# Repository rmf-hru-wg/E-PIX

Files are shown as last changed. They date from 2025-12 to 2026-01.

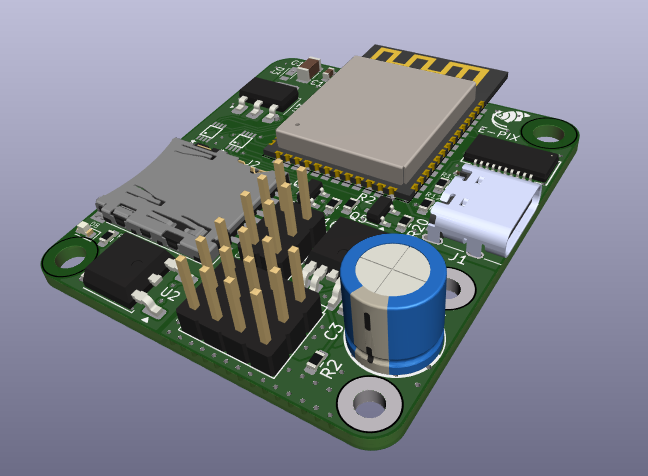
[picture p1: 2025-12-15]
E-PIX/img_front.png

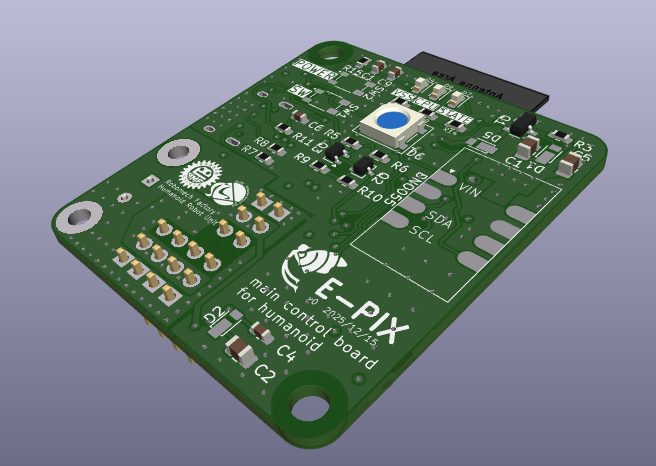
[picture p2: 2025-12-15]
E-PIX/img_back.png

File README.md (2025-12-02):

# Control Board 1

## スペック

- ESP32C3@160MHz WiFi+BT5(BT Classicは非対応)
- ICS変換 × 2
- ADC × 2
- BTS6142D 保護回路+ロードスイッチ
- 9DoF IMU AE-BNO055を裏面に搭載可能

## 設計指針

- できるだけ安く　1000円以下
- できるだけ小さく　40mm×40mm
- ICS変換基板の小型化　10mm×8mm
- 無線を使った遠隔操作　WiFi 2.4GHz IEEE 802.11b/g/n

## 今後の方針

- CPUをラズパイなどにして計算性能やカメラの搭載
- ROS2と繋げる

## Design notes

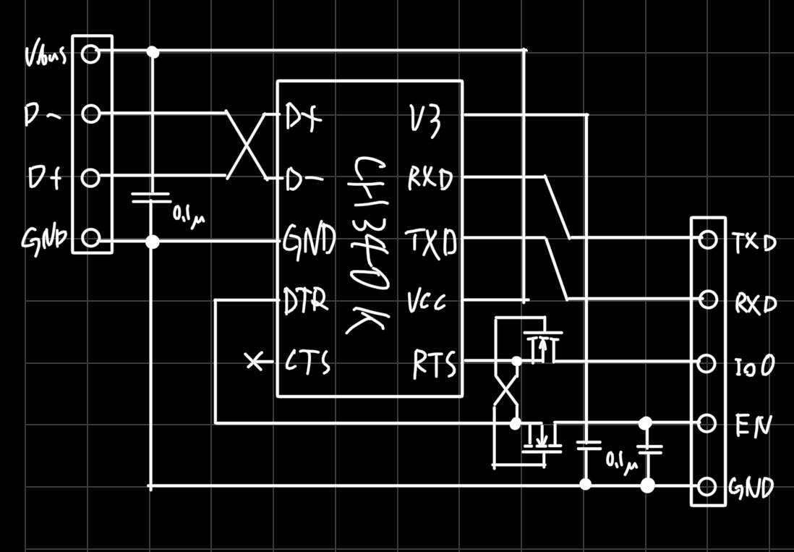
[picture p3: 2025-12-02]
DataSheets/Board/esp32-ch340k.jpeg

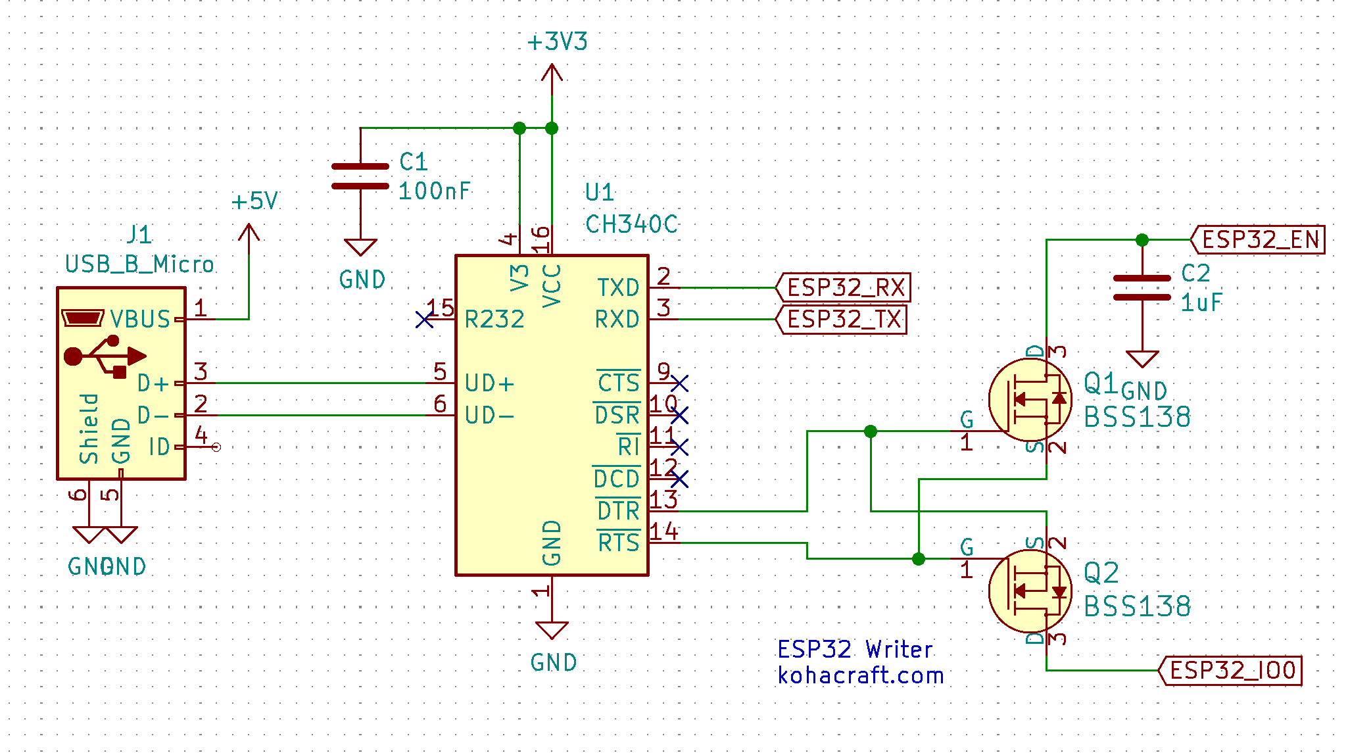
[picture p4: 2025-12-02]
DataSheets/Board/esp32ch340.png

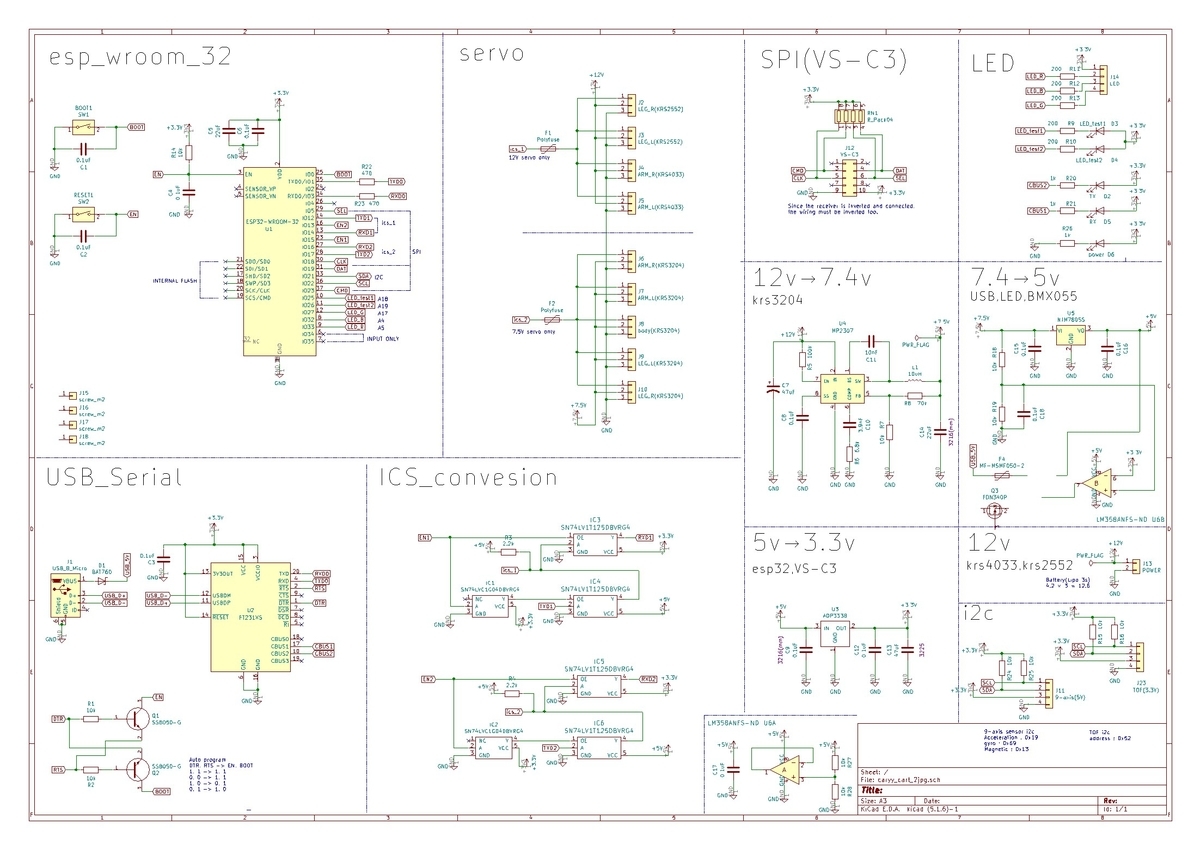
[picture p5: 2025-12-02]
DataSheets/Board/ESP32Kondo.jpg

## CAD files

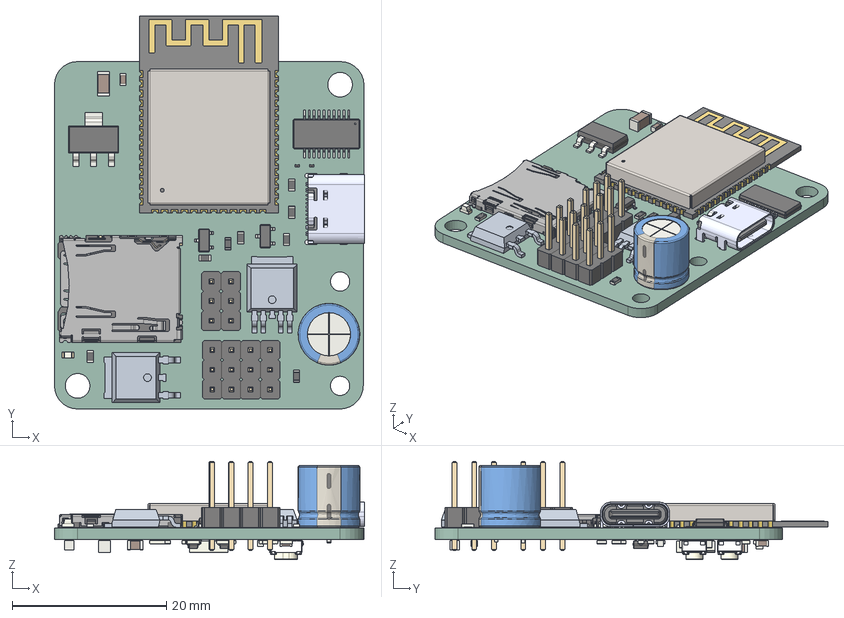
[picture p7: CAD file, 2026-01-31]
E-PIX/E-PIX.step
40.2 x 50.9 x 12.7 mm
C_1206_3216Metric x 2
R_0603_1608Metric x 13
microSD_HC_Hirose_DM3AT-SF-PEJM5
C_0201_0603Metric x 2
C_0603_1608Metric x 6
LED_0603_1608Metric x 3
5077CR-16-SMC2-BK-TR
E-PIX 1.12.1
SOT-23 x 2
C0201_20210301.STEP^C0201_20210301.STEP_Submodel-C0201_part_ DesignRootModel_PCB_ESP32-S3-WROOM-1_V1(2)_PCB_ESP32-S3-WROOM-1_V1 x 14
L0201_20210301.STEP^L0201_20210301.STEP_Submodel-L0201_part_ DesignRootModel_PCB_ESP32-S3-WROOM-1_V1(2)_PCB_ESP32-S3-WROOM-1_V1 x 3
C0402_20210301.STEP^C0402_20210301.STEP_Submodel-C0402_part_ DesignRootModel_PCB_ESP32-S3-WROOM-1_V1(2)_PCB_ESP32-S3-WROOM-1_V1
R0201_20210301.STEP^R0201_20210301.STEP_Submodel-R0201_part_ DesignRootModel_PCB_ESP32-S3-WROOM-1_V1(2)_PCB_ESP32-S3-WROOM-1_V1 x 8
trace_1^Submodel-MINI-ANT-TYPEB_668419613_part_DesignRootModel_PCB_ ESP32-S3-WROOM-1_V1(2)_PCB_ESP32-S3-WROOM-1_V1
DFN1006.STEP^DFN1006.STEP_Submodel-SOD882_part_DesignRootModel_PCB_ ESP32-S3-WROOM-1_V1(2)_PCB_ESP32-S3-WROOM-1_V1
SOP8_rev1_20210308.STEP^SOP8_rev1_20210308.STEP_Submodel-SOP8_1P27_6P6_ part_DesignRootModel_PCB_ESP32-S3-WROOM-1_V1(2)_PCB_ESP32-S3-WROOM-1_V1
XTAL3225_20210301.STEP^XTAL3225_20210301.STEP_Submodel-XTAL3225_part_ DesignRootModel_PCB_ESP32-S3-WROOM-1_V1(2)_PCB_ESP32-S3-WROOM-1_V1
ESP32-S3_20210301.STEP^ESP32-S3_20210301.STEP_Submodel-QFN56_0P4_7_ part_DesignRootModel_PCB_ESP32-S3-WROOM-1_V1(2)_PCB_ESP32-S3-WROOM-1_V1
uid__4-128^DesignRootModel_PCB_ESP32-S3-WROOM-1_V1(2)_PCB_ ESP32-S3-WROOM-1_V1
uid__4-129^DesignRootModel_PCB_ESP32-S3-WROOM-1_V1(2)_PCB_ ESP32-S3-WROOM-1_V1
uid__4-130^DesignRootModel_PCB_ESP32-S3-WROOM-1_V1(2)_PCB_ ESP32-S3-WROOM-1_V1
uid__4-149^DesignRootModel_PCB_ESP32-S3-WROOM-1_V1(2)_PCB_ ESP32-S3-WROOM-1_V1
uid__4-150^DesignRootModel_PCB_ESP32-S3-WROOM-1_V1(2)_PCB_ ESP32-S3-WROOM-1_V1
uid__4-151^DesignRootModel_PCB_ESP32-S3-WROOM-1_V1(2)_PCB_ ESP32-S3-WROOM-1_V1
uid__4-167^DesignRootModel_PCB_ESP32-S3-WROOM-1_V1(2)_PCB_ ESP32-S3-WROOM-1_V1
uid__4-168^DesignRootModel_PCB_ESP32-S3-WROOM-1_V1(2)_PCB_ ESP32-S3-WROOM-1_V1
uid__4-169^DesignRootModel_PCB_ESP32-S3-WROOM-1_V1(2)_PCB_ ESP32-S3-WROOM-1_V1
uid__1-279^DesignRootModel_PCB_ESP32-S3-WROOM-1_V1(2)_PCB_ ESP32-S3-WROOM-1_V1
uid__1-280^DesignRootModel_PCB_ESP32-S3-WROOM-1_V1(2)_PCB_ ESP32-S3-WROOM-1_V1
uid__1-292^DesignRootModel_PCB_ESP32-S3-WROOM-1_V1(2)_PCB_ ESP32-S3-WROOM-1_V1
uid__1-298^DesignRootModel_PCB_ESP32-S3-WROOM-1_V1(2)_PCB_ ESP32-S3-WROOM-1_V1
uid__1-299^DesignRootModel_PCB_ESP32-S3-WROOM-1_V1(2)_PCB_ ESP32-S3-WROOM-1_V1
uid__1-300^DesignRootModel_PCB_ESP32-S3-WROOM-1_V1(2)_PCB_ ESP32-S3-WROOM-1_V1
uid__1-301^DesignRootModel_PCB_ESP32-S3-WROOM-1_V1(2)_PCB_ ESP32-S3-WROOM-1_V1
uid__1-304^DesignRootModel_PCB_ESP32-S3-WROOM-1_V1(2)_PCB_ ESP32-S3-WROOM-1_V1
uid__1-305^DesignRootModel_PCB_ESP32-S3-WROOM-1_V1(2)_PCB_ ESP32-S3-WROOM-1_V1
uid__1-308^DesignRootModel_PCB_ESP32-S3-WROOM-1_V1(2)_PCB_ ESP32-S3-WROOM-1_V1
uid__1-310^DesignRootModel_PCB_ESP32-S3-WROOM-1_V1(2)_PCB_ ESP32-S3-WROOM-1_V1
uid__1-311^DesignRootModel_PCB_ESP32-S3-WROOM-1_V1(2)_PCB_ ESP32-S3-WROOM-1_V1
uid__1-325^DesignRootModel_PCB_ESP32-S3-WROOM-1_V1(2)_PCB_ ESP32-S3-WROOM-1_V1
uid__1-334^DesignRootModel_PCB_ESP32-S3-WROOM-1_V1(2)_PCB_ ESP32-S3-WROOM-1_V1
uid__1-338^DesignRootModel_PCB_ESP32-S3-WROOM-1_V1(2)_PCB_ ESP32-S3-WROOM-1_V1
uid__1-339^DesignRootModel_PCB_ESP32-S3-WROOM-1_V1(2)_PCB_ ESP32-S3-WROOM-1_V1
uid__1-340^DesignRootModel_PCB_ESP32-S3-WROOM-1_V1(2)_PCB_ ESP32-S3-WROOM-1_V1
uid__1-343^DesignRootModel_PCB_ESP32-S3-WROOM-1_V1(2)_PCB_ ESP32-S3-WROOM-1_V1
uid__1-344^DesignRootModel_PCB_ESP32-S3-WROOM-1_V1(2)_PCB_ ESP32-S3-WROOM-1_V1
uid__1-345^DesignRootModel_PCB_ESP32-S3-WROOM-1_V1(2)_PCB_ ESP32-S3-WROOM-1_V1
uid__1-352^DesignRootModel_PCB_ESP32-S3-WROOM-1_V1(2)_PCB_ ESP32-S3-WROOM-1_V1
uid__1-354^DesignRootModel_PCB_ESP32-S3-WROOM-1_V1(2)_PCB_ ESP32-S3-WROOM-1_V1
uid__1-355^DesignRootModel_PCB_ESP32-S3-WROOM-1_V1(2)_PCB_ ESP32-S3-WROOM-1_V1
uid__1-357^DesignRootModel_PCB_ESP32-S3-WROOM-1_V1(2)_PCB_ ESP32-S3-WROOM-1_V1
uid__1-358^DesignRootModel_PCB_ESP32-S3-WROOM-1_V1(2)_PCB_ ESP32-S3-WROOM-1_V1
uid__1-359^DesignRootModel_PCB_ESP32-S3-WROOM-1_V1(2)_PCB_ ESP32-S3-WROOM-1_V1
uid__1-364^DesignRootModel_PCB_ESP32-S3-WROOM-1_V1(2)_PCB_ ESP32-S3-WROOM-1_V1
uid__1-365^DesignRootModel_PCB_ESP32-S3-WROOM-1_V1(2)_PCB_ ESP32-S3-WROOM-1_V1
uid__1-371^DesignRootModel_PCB_ESP32-S3-WROOM-1_V1(2)_PCB_ ESP32-S3-WROOM-1_V1
uid__1-375^DesignRootModel_PCB_ESP32-S3-WROOM-1_V1(2)_PCB_ ESP32-S3-WROOM-1_V1
uid__1-376^DesignRootModel_PCB_ESP32-S3-WROOM-1_V1(2)_PCB_ ESP32-S3-WROOM-1_V1
uid__1-378^DesignRootModel_PCB_ESP32-S3-WROOM-1_V1(2)_PCB_ ESP32-S3-WROOM-1_V1
uid__1-379^DesignRootModel_PCB_ESP32-S3-WROOM-1_V1(2)_PCB_ ESP32-S3-WROOM-1_V1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

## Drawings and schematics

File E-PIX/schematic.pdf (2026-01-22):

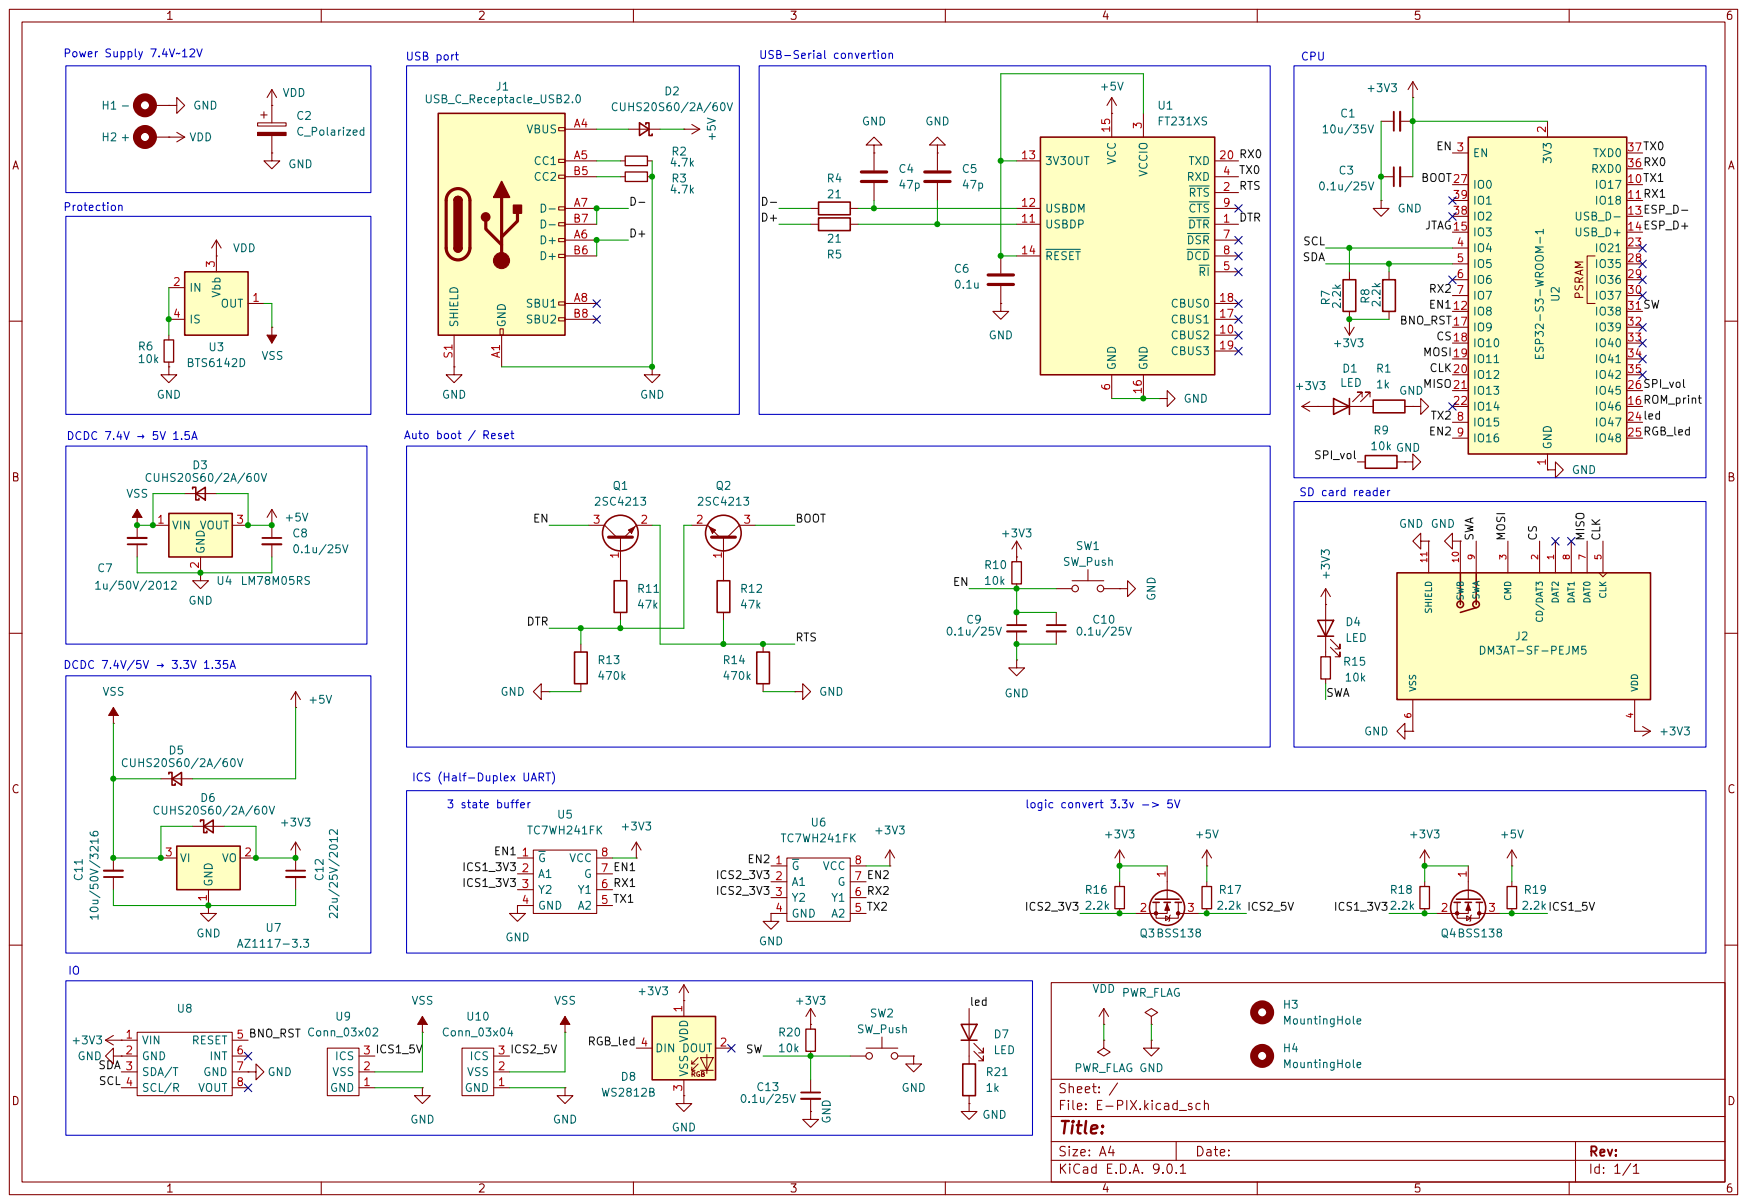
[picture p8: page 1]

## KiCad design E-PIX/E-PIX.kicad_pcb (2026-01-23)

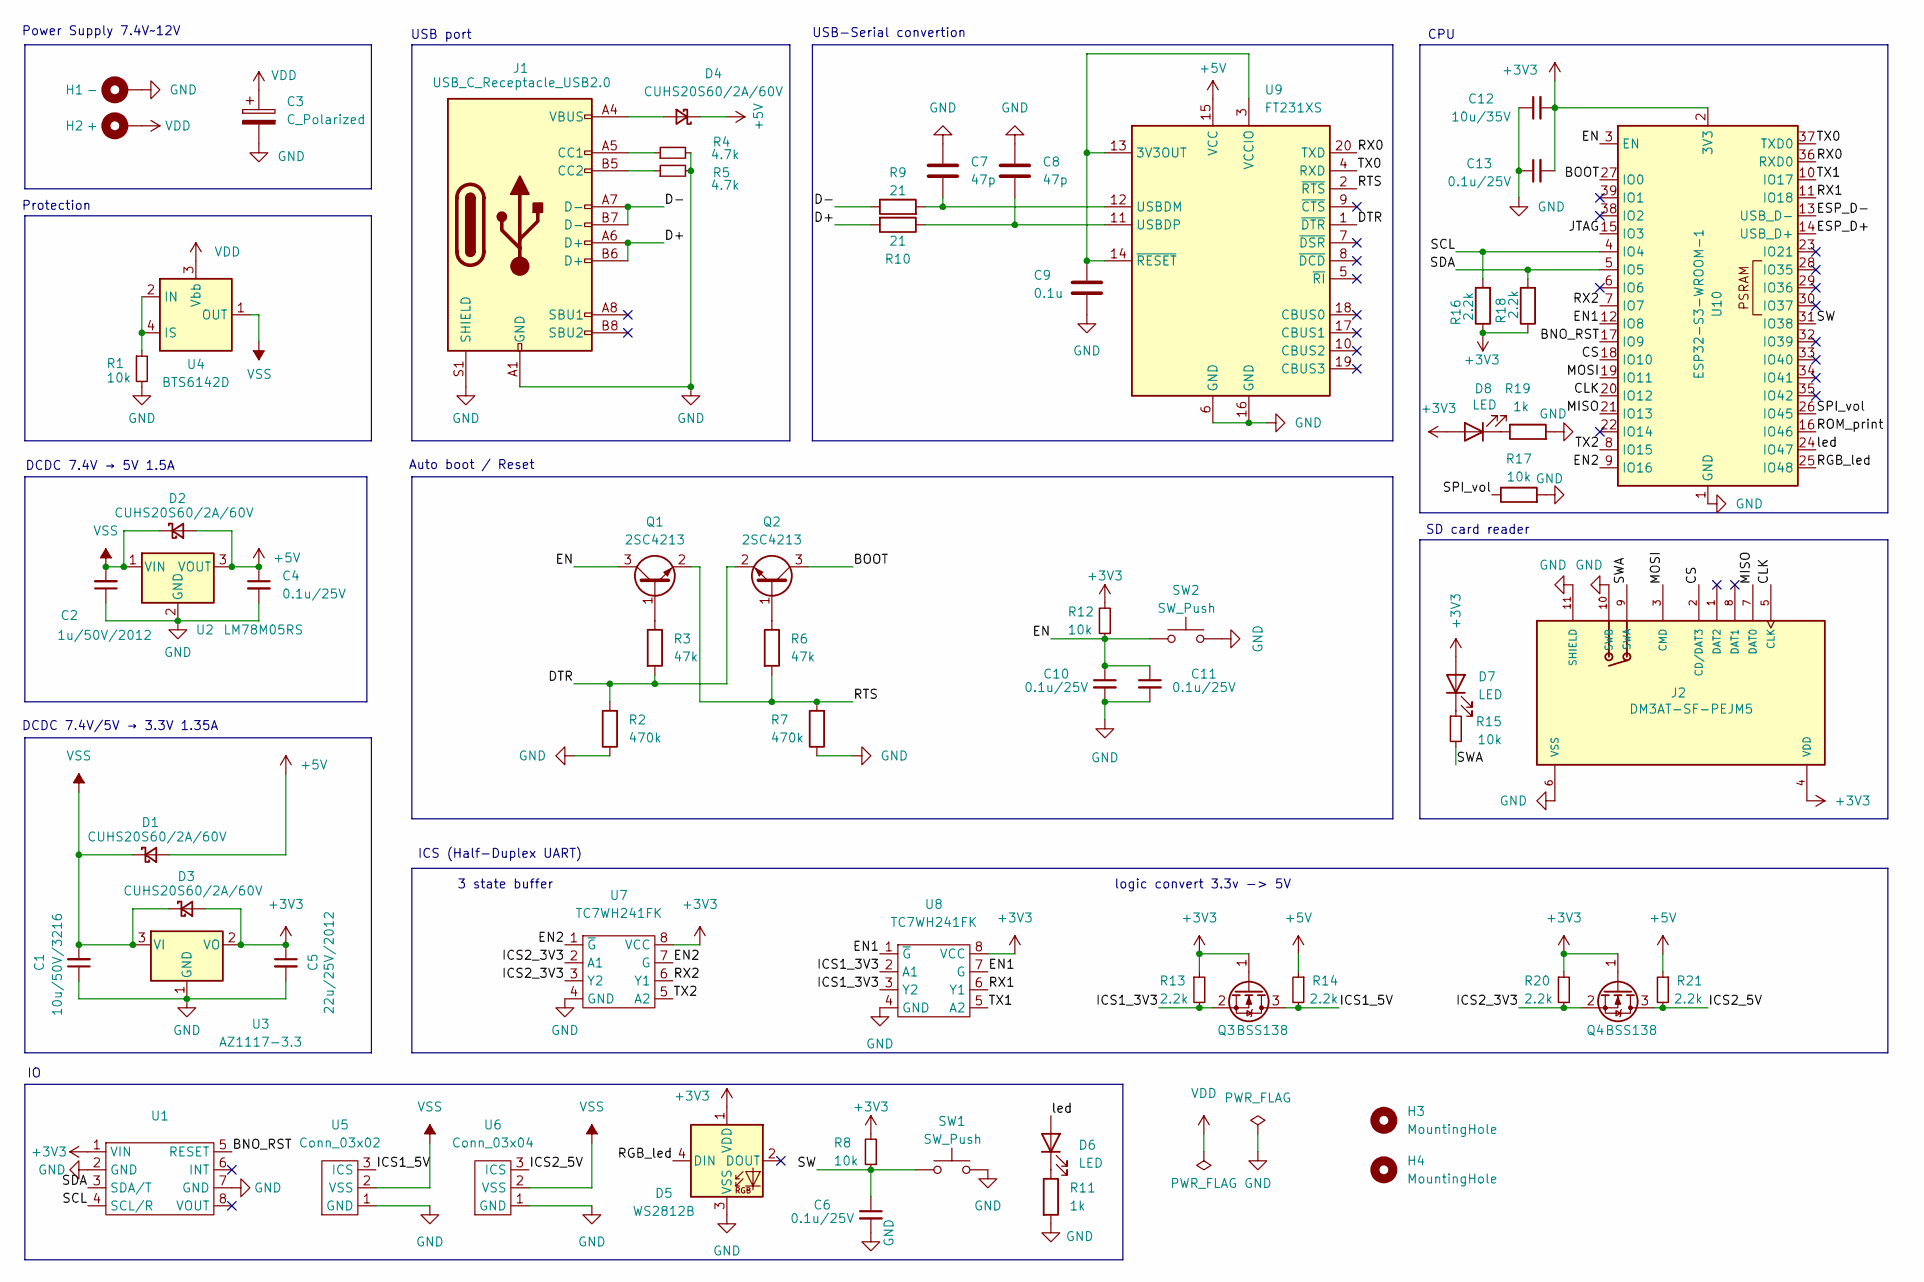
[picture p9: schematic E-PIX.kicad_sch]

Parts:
C1: 10u/50V/3216; C_1206_3216Metric
C2: 1u/50V/2012; C_0805_2012Metric
C3: C_Polarized; CP_Radial_D8.0mm_P3.50mm
C4, C6, C10, C11, C13: 0.1u/25V; C_0603_1608Metric
C5: 22u/25V/2012; C_0805_2012Metric
C7, C8: 47p; C_0201_0603Metric
C9: 0.1u; C_0603_1608Metric
C12: 10u/35V; C_1206_3216Metric
D1, D2, D3, D4: CUHS20S60/2A/60V; Diode_US2H
D5: WS2812B; LED_WS2812B_PLCC4_5.0x5.0mm_P3.2mm
D6, D7, D8: LED; LED_0603_1608Metric
H1: -; MountingHole_2.5mm_Pad
H2: +; MountingHole_2.5mm_Pad
H3, H4: MountingHole; MountingHole_3.2mm_M3_DIN965
J1: USB_C_Receptacle_USB2.0; USB_C_Receptacle_XKB_U262-16XN-4BVC11_with_model
J2: DM3AT-SF-PEJM5; microSD_HC_Hirose_DM3AT-SF-PEJM5; PARTREV 20200913
Q1, Q2: 2SC4213; SOT-323_SC-70
Q3, Q4: BSS138; SOT-23
R1, R8, R12, R15, R17: 10k; R_0603_1608Metric
R2, R7: 470k; R_0603_1608Metric
R3, R6: 47k; R_0805_2012Metric
R4, R5: 4.7k; R_0805_2012Metric
R9, R10: 21; R_0603_1608Metric
R11, R19: 1k; R_0805_2012Metric
R13, R14, R20, R21: 2.2k; R_0603_1608Metric
R16, R18: 2.2k; R_0805_2012Metric
SW1, SW2: SW_Push; SW_SKRPACE010
U1: BNO055
U2: LM78M05RS; TO-252-2
U3: AZ1117-3.3; SOT-223-3_TabPin2
U4: BTS6142D; TO-252-4
U5: Conn_03x02; PinHeader_03x02_P2.54mm_Vertical
U6: Conn_03x04; PinHeader_03x04_P2.54mm_Vertical
U7, U8: TC7WH241FK; US-8
U9: FT231XS; SSOP-20_3.9x8.7mm_P0.635mm
U10: ESP32-S3-WROOM-1

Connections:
+3V3: C5.1, C12.2, C13.2, D3.2 (A), D5.1 (VDD), D7.2 (A), D8.2 (A), J2.4 (VDD), Q3.1 (G), Q4.1 (G), R8.2, R12.2, R13.1, R16.1, R18.1, R20.1, U1.1 (VIN), U3.2 (VO), U7.8 (VCC), U8.8 (VCC), U10.2 (3V3)
+5V: C4.1, D1.2 (A), D2.2 (A), D4.1 (K), R14.1, R21.1, U2.3 (VOUT), U9.15 (VCC)
/BNO_RST: U1.5 (RESET), U10.17 (IO9)
/BOOT: Q2.3 (C), U10.27 (IO0)
/CLK: J2.5 (CLK), U10.20 (IO12)
/CS: J2.2 (CD/DAT3), U10.18 (IO10)
/D+: J1.A6 (D+), J1.B6 (D+), R10.2
/D-: J1.A7 (D-), J1.B7 (D-), R9.1
/DTR: Q2.2 (E), R2.2, R3.2, U9.1 (~DTR)
/EN: C10.1, C11.1, Q1.3 (C), R12.1, SW2.1, U10.3 (EN)
/EN1: U8.1 (~G), U8.7 (G), U10.12 (IO8)
/EN2: U7.1 (~G), U7.7 (G), U10.9 (IO16)
/ESP_D+: U10.14 (USB_D+)
/ESP_D-: U10.13 (USB_D-)
/ICS1_3V3: Q3.2 (S), R13.2, U8.2 (A1), U8.3 (Y2)
/ICS1_5V: Q3.3 (D), R14.2, U5.3 (ICS)
/ICS2_3V3: Q4.2 (S), R20.2, U7.2 (A1), U7.3 (Y2)
/ICS2_5V: Q4.3 (D), R21.2, U6.3 (ICS)
/JTAG: U10.15 (IO3)
/MISO: J2.7 (DAT0), U10.21 (IO13)
/MOSI: J2.3 (CMD), U10.19 (IO11)
/RGB_led: D5.4 (DIN), U10.25 (IO48)
/ROM_print: U10.16 (IO46)
/RTS: Q1.2 (E), R6.2, R7.2, U9.2 (~RTS)
/RX0: U9.20 (TXD), U10.36 (RXD0)
/RX1: U8.6 (Y1), U10.11 (IO18)
/RX2: U7.6 (Y1), U10.7 (IO7)
/SCL: R16.2, U1.4 (SCL/R), U10.4 (IO4)
/SDA: R18.2, U1.3 (SDA/T), U10.5 (IO5)
/SPI_vol: R17.1, U10.26 (IO45)
/SW: C6.1, R8.1, SW1.1, U10.31 (IO38)
/SWA: J2.9 (SWA), R15.2
/TX0: U9.4 (RXD), U10.37 (TXD0)
/TX1: U8.5 (A2), U10.10 (IO17)
/TX2: U7.5 (A2), U10.8 (IO15)
/led: D6.2 (A), U10.24 (IO47)
GND: C1.1, C2.1, C3.2, C4.2, C5.2, C6.2, C7.1, C8.1, C9.2, C10.2, C11.2, C12.1, C13.1, D5.3 (VSS), H1.1, J1.A1 (GND), J1.A12 (GND), J1.B1 (GND), J1.B12 (GND), J1.S1 (SHIELD), J2.6 (VSS), J2.10 (SWB), J2.11 (SHIELD), R1.2, R2.1, R4.2, R5.2, R7.1, R11.2, R17.2, R19.2, SW1.2, SW2.2, U1.2 (GND), U1.7 (GND), U2.2 (GND), U3.1 (GND), U5.1 (GND), U6.1 (GND), U7.4 (GND), U8.4 (GND), U9.6 (GND), U9.16 (GND), U10.1 (GND), U10.40 (GND), U10.41 (GND)
unnamed: D4.2 (A), J1.A4 (VBUS), J1.A9 (VBUS), J1.B4 (VBUS), J1.B9 (VBUS)
unnamed: D6.1 (K), R11.1
unnamed: D7.1 (K), R15.1
unnamed: D8.1 (K), R19.1
unnamed: J1.A5 (CC1), R4.1
unnamed: J1.B5 (CC2), R5.1
unnamed: Q1.1 (B), R3.1
unnamed: Q2.1 (B), R6.1
unnamed: R1.1, U4.2 (IN), U4.4 (IS)
unnamed: C9.1, U9.3 (VCCIO), U9.13 (3V3OUT), U9.14 (~RESET)
unnamed: C7.2, R9.2, U9.12 (USBDM)
unnamed: C8.2, R10.1, U9.11 (USBDP)
VDD: C3.1, H2.1, U4.3 (Vbb)
VSS: C1.2, C2.2, D1.1 (K), D2.1 (K), D3.1 (K), U2.1 (VIN), U3.3 (VI), U4.1 (OUT), U4.5 (OUT), U5.2 (VSS), U6.2 (VSS)

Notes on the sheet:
USB-Serial convertion
logic convert 3.3v -> 5V
ICS (Half-Duplex UART)
3 state buffer
CPU
SD card reader
Auto boot / Reset
Protection
DCDC 7.4V → 5V 1.5A
DCDC 7.4V/5V → 3.3V 1.35A
Power Supply 7.4V~12V
USB port

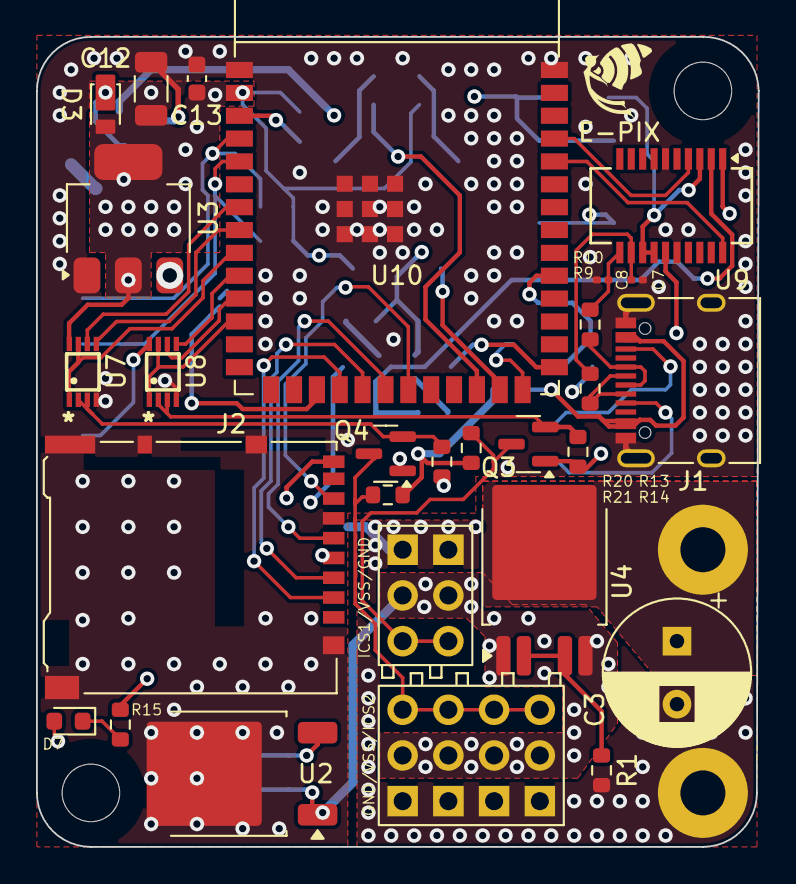
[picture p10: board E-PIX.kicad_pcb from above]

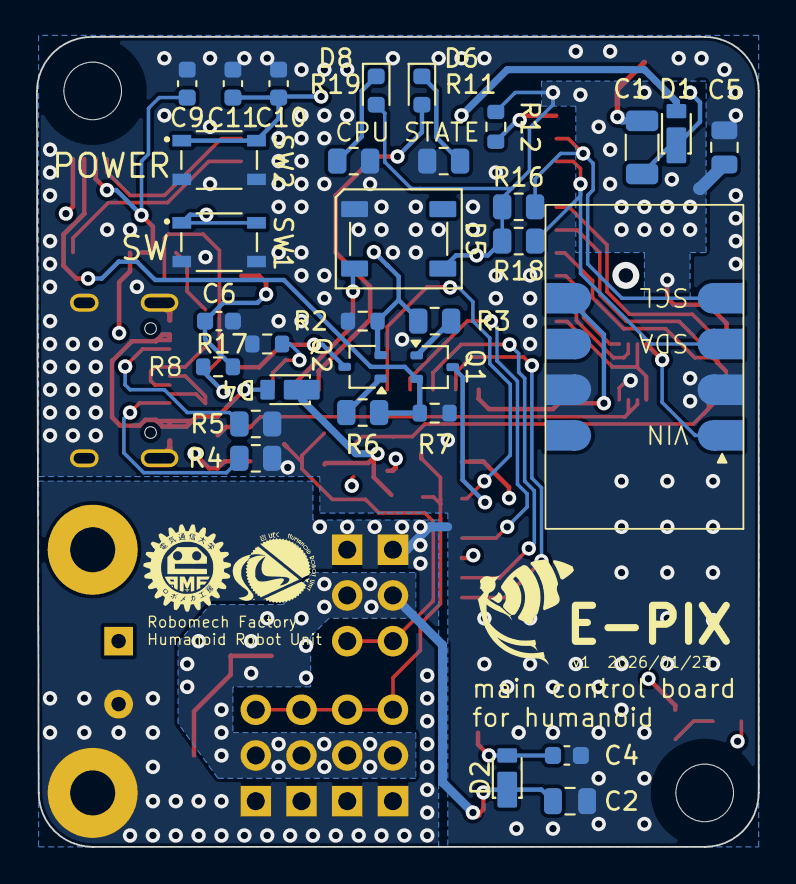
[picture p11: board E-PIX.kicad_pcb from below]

Board: 6 copper layers, 40.1 x 45.0 mm, 64 parts (32 on the bottom side), 47 nets.

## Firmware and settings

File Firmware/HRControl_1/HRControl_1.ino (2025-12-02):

// #include <WiFi.h>
#include "IcsHardSerialClass.h"
#include "pin.h"

#define BAUDRATE 115200
#define TIMEOUT 1000

IcsHardSerialClass krs1(&Serial0, EN1, BAUDRATE, TIMEOUT, RX1, TX1);
IcsHardSerialClass krs2(&Serial1, EN2, BAUDRATE, TIMEOUT, RX2, TX2);

void setup() {
  Serial.begin();
  krs1.begin();
  krs2.begin();
}
void loop() {
    //Serial.println("ok");
    //delay(100);
    for(int i=4000;i<11000;i+=100){
      int now1 = krs1.setPos(0, i);
      int now2 = krs2.setPos(0, i);
      Serial.printf("%d %d\r\n", now1, now2);
      delay(10);
    }
    krs1.setPos(0, 4000);
    krs2.setPos(0, 4000);
    delay(1000);
    /*
    //位置指令　ID:0サーボを7500へ 中央
    delay(500); //0.5秒待つ
    krs.setPos(0,9500); //位置指令　ID:0サーボを9500へ 右
    delay(500); //0.5秒待つ
    krs.setPos(0,7500); //位置指令　ID:0サーボを7500へ 中央
    delay(500); //0.5秒待つ
    krs.setPos(0,5500); //位置指令　ID:0サーボを5500へ 左
    delay(500);
    */
}

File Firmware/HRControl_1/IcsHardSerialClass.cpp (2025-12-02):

/**
*	@file IcsHardSerialClass.cpp
*	@brief ICS3.5/3.6 arduino library use HardwareSerial
*	@author Kondo Kagaku Co.,Ltd.
*	@date	2017/12/27
*	@version 2.0.0
*	@copyright &copy; Kondo Kagaku Co.,Ltd. 2017
**/


#include <Arduino.h>
#include "IcsHardSerialClass.h"

/**
*	@brief コンストラクタ
**/
IcsHardSerialClass::IcsHardSerialClass()
{
	
}




/**
*	@brief コンストラクタ
*	@param[in] *icsSerial ICSに設定するUART(HardwareSerial型のポインタ)
* 	@param[in] enpin 送受信切替えピンのピン番号
**/
IcsHardSerialClass::IcsHardSerialClass(HardwareSerial *icsSerial,byte enpin)
{
  icsHardSerial = icsSerial;
  enPin = enpin;
}

/**
* @brief コンストラクタ
* @param[in] *hardSerial ICSに設定するUART(HardwareSerial型のポインタ)
* @param[in] enpin 送受信切替えピンのピン番号
* @param[in] baudrate サーボの通信速度
* @param[in] timeout 受信タイムアウト(ms)

**/
IcsHardSerialClass::IcsHardSerialClass(HardwareSerial *hardSerial,byte enpin, long baudrate, int timeout, int rxpin, int txpin)
{
  icsHardSerial = hardSerial;
  enPin = enpin;
  baudRate = baudrate;
  timeOut = timeout;
  rxPin = rxpin;
  txPin = txpin;
}

/**
* @brief デストラクタ
* @post 使用していたのicsHardSerialを開放します
**/
IcsHardSerialClass::~IcsHardSerialClass()
{
  if (icsHardSerial)  //定義してあったらSerialを解放する
  {
    icsHardSerial->end();
  }
}



//初期設定 　void setup()へ　///////////////////////////////////////////////////////////////////////////////
/**
* @brief 通信の初期設定
* @retval true 通信設定完了
* @retval false 通信設定失敗
* @attention Serialの設定、通信速度、タイムアウトは事前に設定してある事
**/
bool IcsHardSerialClass::begin()
{
  if (icsHardSerial == nullptr)
  {
    return false;
  }

  icsHardSerial->begin(baudRate,SERIAL_8E1, rxPin, txPin);
  icsHardSerial->setTimeout(timeOut);
  pinMode(enPin, OUTPUT);
  enLow();
  
	
  return true;
}

/**
* @brief 通信の初期設定
* @param[in] baudrate ICSの通信速度(115200,625000,1250000(1.25M)bps)
* @param[in] timeout 受信タイムアウト(ms)
* @retval true 通信設定完了
* @retval false 通信設定失敗
* @attention UARTピンおよび送受信切替えピンは設定してある事
**/
bool IcsHardSerialClass::begin(long baudrate,int timeout)
{
  baudRate =  baudrate;
  timeOut  = timeout;
  return begin();
}

/**
* @brief 通信の初期設定
* @param[in] *serial ICSに設定するUART(HardwareSerial型のポインタ)
* @param[in] enpin 送受信切替えピンのピン番号
* @param[in] baudrate ICSの通信速度(115200,625000,1250000(1.25M)bps)
* @param[in] timeout 受信タイムアウト(ms)
* @retval true 通信設定完了
* @retval false 通信設定失敗
**/
bool IcsHardSerialClass::begin(HardwareSerial *serial,int enpin,long baudrate,int timeout)
{
  icsHardSerial = serial;
  enPin = enpin;
  baudRate =  baudrate;
  timeOut  = timeout;
  return begin();
}



//データ送受信 /////////////////////////////////////////////////////////////////////////////////////////////
/**
* @brief ICS通信の送受信
* @param[in,out] *txBuf
* @param[in] txLen
* @param[out] *rxBuf 受信格納バッファ
* @param[in] rxLen  受信データ数
* @retval true 通信成功
* @retval false 通信失敗
* @attention 送信データ数、受信データ数はコマンドによって違うので注意する
* @date 2020/02/18 protectedからpublicに変更
**/
bool IcsHardSerialClass::synchronize(byte *txBuf, byte txLen, byte *rxBuf, byte rxLen)
{
	int rxSize; //受信数

	//シリアル初期化確認
  
	if(icsHardSerial == nullptr )
	{
		return false;
	}

	icsHardSerial->flush(); //待つ
	enHigh(); //送信切替
	icsHardSerial->write(txBuf, txLen);
	icsHardSerial->flush();   //待つ
	
	while (icsHardSerial->available() > 0) //受信バッファを消す
	{
		// buff = icsSerial->read();	//空読み
		icsHardSerial->read();		//空読み
	}

	enLow();  //受信切替


	rxSize = icsHardSerial->readBytes(rxBuf, rxLen);

	if (rxSize != rxLen) //受信数確認
	{
		return false;
	}
	return true;

	
}

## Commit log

2025-12-02 add SD card mod
    [DM3AT-SF-PEJM5.step, E-PIX.kicad_sch]
2025-12-02 complete main function. start checking
    [E-PIX.kicad_sch]
2025-12-03 finish eeschema. anotate numbers in next step
    [E-PIX.kicad_sch, SKRPACE010.stp]
2025-12-03 finish eeschema. start placing tips
    [5077CR-16-SMC2-BK-TR.STEP, E-PIX.kicad_pcb, E-PIX.kicad_sch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]
2025-12-05 place 3v3 reg and USB-TTY serial
    [E-PIX.kicad_pcb, E-PIX.kicad_sch]
2025-12-05 update some pin mappings of ESP
    [E-PIX.kicad_pcb, E-PIX.kicad_sch]
2025-12-11 place all the tips
    [E-PIX.kicad_pcb, E-PIX.kicad_sch]
2025-12-11 adjust all the footprints. start trying free routing
    [E-PIX.kicad_pcb]
2025-12-11 route main wires
    [E-PIX.dsn, E-PIX.kicad_pcb]
2025-12-11 failed free routing
    [E-PIX.dsn, E-PIX.kicad_pcb]
2025-12-11 move some tips
    [E-PIX.dsn, E-PIX.kicad_pcb, E-PIX.kicad_sch]
2025-12-12 successfly apply free routing
    [E-PIX.kicad_pcb]
2025-12-12 create bear
    [E-PIX.kicad_pcb, freerouting.dsn]
2025-12-15 put silkscreen
    [E-PIX.kicad_pcb]
2025-12-15 create logo mark.
    [E-PIX.ipt, E-PIX.kicad_pcb, SKRPACE010.ipt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]
2025-12-15 update silkscreen. ordered.
    [E-PIX.kicad_pcb]
2025-12-15 update gitignore
    [5077CR-16-SMC2-BK-TR.STEP, DM3AT-SF-PEJM5.step, E-PIX.ipt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]
2025-12-15 add pdf schematic and img
    [E-PIX.kicad_pcb]
2025-12-15 add step
    [E-PIX.step]
2026-01-19 add tests
    [E-PIX.kicad_pcb, E-PIX.kicad_sch]
2026-01-20 add test codes for boards
2026-01-22 fix sketch error
    [5077CR-16-SMC2-BK-TR.ipt, C0201_20210301.STEP^C0201_20210301.STEP_Submodel-C0201_part_DesignRootModel_PCB_ESP32-S3-WROOM-1_V1(2)_PCB_ESP32-S3-WROOM-1_V1.ipt, C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]
2026-01-22 correct all errors. waiting for check. (order tomorrow)
    [E-PIX.kicad_pcb, E-PIX.kicad_sch]
2026-01-23 go thorough last check. order
    [E-PIX.kicad_pcb, E-PIX.kicad_sch]
2026-01-31 check all functions. Confirm both serial1 and serial2
    [E-PIX.step]
2026-02-02 add code to check all motors
2026-02-05 confirm motor movement
